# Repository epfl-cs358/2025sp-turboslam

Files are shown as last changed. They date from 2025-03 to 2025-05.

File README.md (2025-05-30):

# CS-358 - Making Intelligent Things 2025 Spring

## Project: TurboSLAM - Fast Autonomous Car using Simultaneous Localization and Mapping

TLDR: If you just want to run the thing, see section [3D SLAM (LiDAR odometry only)](#3d-slam-lidar-odometry-only).

## Contributors

- Vincent Palma
- Loris Baldisserotto
- Ivan Dylevskiy
- Ilian Changkakoti
- Sarah Lim

[Google Doc](https://docs.google.com/document/d/1Hz-CrI_mGBuuY4Cr6uao3CeAetyIk8hIU1p6bzpezqY/edit?usp=sharing)

[Project Proposal](https://www.overleaf.com/read/mtyzjbnkwfxt#540f41)

## Project Overview

This project aims to develop an autonomous system for Simultaneous Localization and Mapping (SLAM) using a 2D LiDAR sensor mounted on a servo motor. The system is designed to map an environment and navigate to given coordinates while avoiding obstacles. The project is based on modifying a **Tamiya Blitzer Beetle** RC car, replacing its original control system with an ESP32 microcontroller.

## Table of Contents

- [Description](#description)
- [User Stories](#user-stories)
- [Component List](#component-list)
- [First Idea of the Mechanical Build](#first-idea-of-the-mechanical-build)
- [How to Assemble](#how-to-assemble)
- [How to Run](#how-to-run)
- [Software](#software)
- [Expected Challenges & Solutions](#expected-challenges--solutions)
- [Evaluation Metrics](#evaluation-metrics)
- [Bill of Materials](#bill-of-materials)

## Description

The system consists of two main phases:

1. **Mapping Phase:** The robot explores the environment while the LiDAR sensor scans at multiple angles using a servo motor, creating a 3D map from 2D slices.

2. **Navigation Phase:** The system autonomously moves towards a user-specified target, avoiding dynamic obstacles in real-time.

The **ESP32** microcontroller handles remote communication and data processing, making the project a cost-effective solution for indoor and outdoor navigation applications.

## Component List

| Component | Info |
| --- | --- |
| Tamiya Blitzer Beetle | [Manual](https://www.tamiyausa.com/media/files/58502ml-829-5367.pdf) |
| RPLIDAR C1 | [Datasheet](https://d229kd5ey79jzj.cloudfront.net/3157/SLAMTEC_rplidar_datasheet_C1_v1.0_en.pdf), [SDK](https://github.com/Slamtec/rplidar_sdk), [Wiki](https://www.waveshare.com/wiki/RPLIDAR_C1) |
| ESP32-S3 Microcontroller (x2) | [Datasheet](https://cdn-shop.adafruit.com/product-files/5477/esp32-s3_datasheet_en.pdf) |
| DMS15 Servo (x2) | [Wiki](https://wiki.dfrobot.com/DSS-M15S_270%C2%B0_15KG_DF_Metal_Servo_with_Analog_Feedback_SKU__SER0044) |
| BNO086 IMU | [Datasheet](https://docs.sparkfun.com/SparkFun_VR_IMU_Breakout_BNO086_QWIIC/assets/component_documentation/BNO080_085-Datasheet_v1.16.pdf) |
| AS5600 Encoder | [Datasheet](https://files.seeedstudio.com/wiki/Grove-12-bit-Magnetic-Rotary-Position-Sensor-AS5600/res/Magnetic%20Rotary%20Position%20Sensor%20AS5600%20Datasheet.pdf) |
| HC-SR04 Ultrasonic sensor | [Datasheet](https://handsontec.com/dataspecs/sensor/SR-04-Ultrasonic.pdf) |
| NEO-6M-V2 GPS | [Datasheet](https://content.u-blox.com/sites/default/files/products/documents/NEO-6_DataSheet_%28GPS.G6-HW-09005%29.pdf) |
| 540J Motor | [Datasheet](https://asset.conrad.com/media10/add/160267/c1/-/en/001385115DS01/adatlap-1385115-540-es-motor-reely-532114c.pdf) |
| THW-1060-RTR ESC | [Datasheet](https://www.hobbywing.com/en/uploads/file/20221015/f60b7ebe160a7b283927ae8916d36763.pdf) |
| LM2596 Buck converter | [Datasheet](https://www.ti.com/lit/ds/symlink/lm2596.pdf) |
| 7.2V Battery | [Product Page](https://www.galaxus.ch/fr/s5/product/gens-ace-modelisme-dune-batterie-720-v-5000-mah-batterie-rc-9459930) |

## First Idea of the Mechanical Build

The original car chassis was unsuitable for mounting sensors, so we built a three-layer structure:

### Base Layer: Chassis

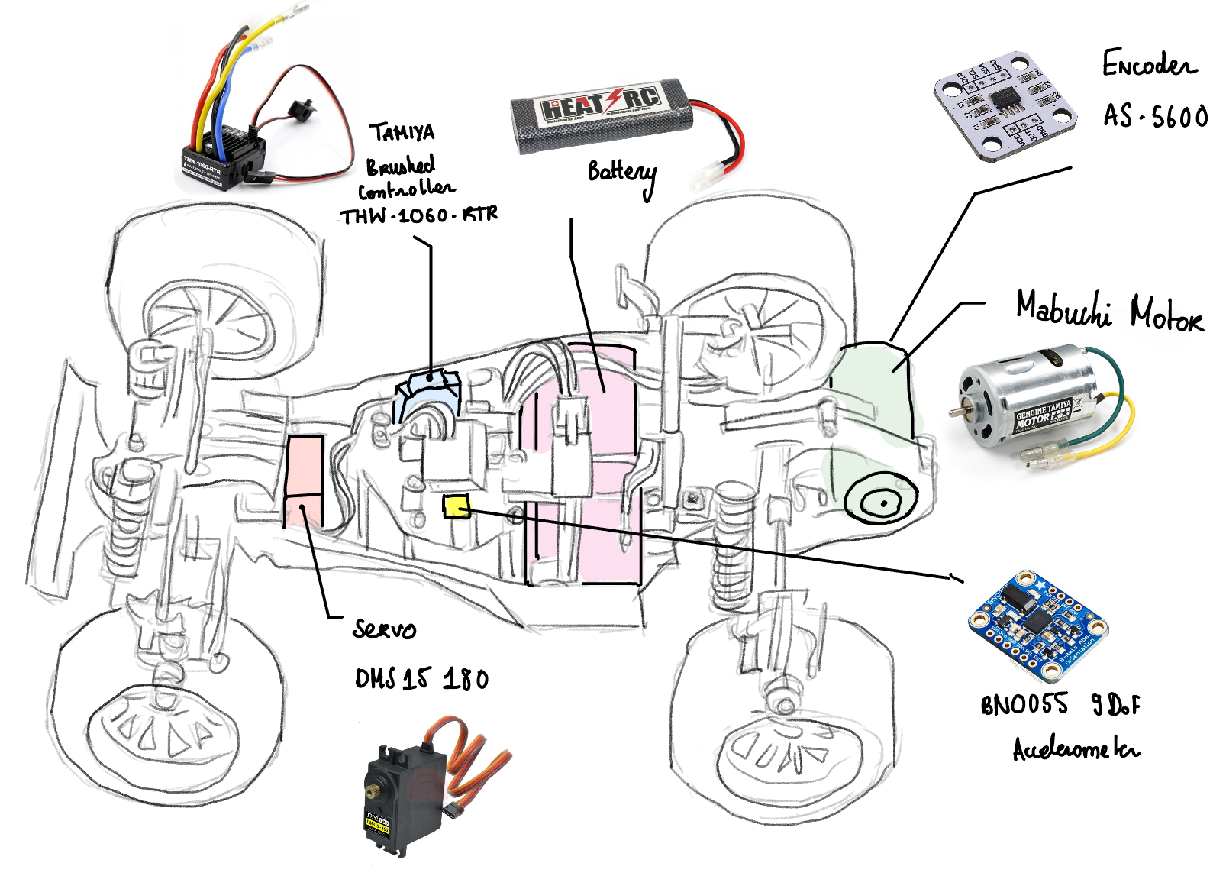
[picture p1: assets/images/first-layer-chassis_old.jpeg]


### Middle Layer: Microcontroller & Electronics Mount

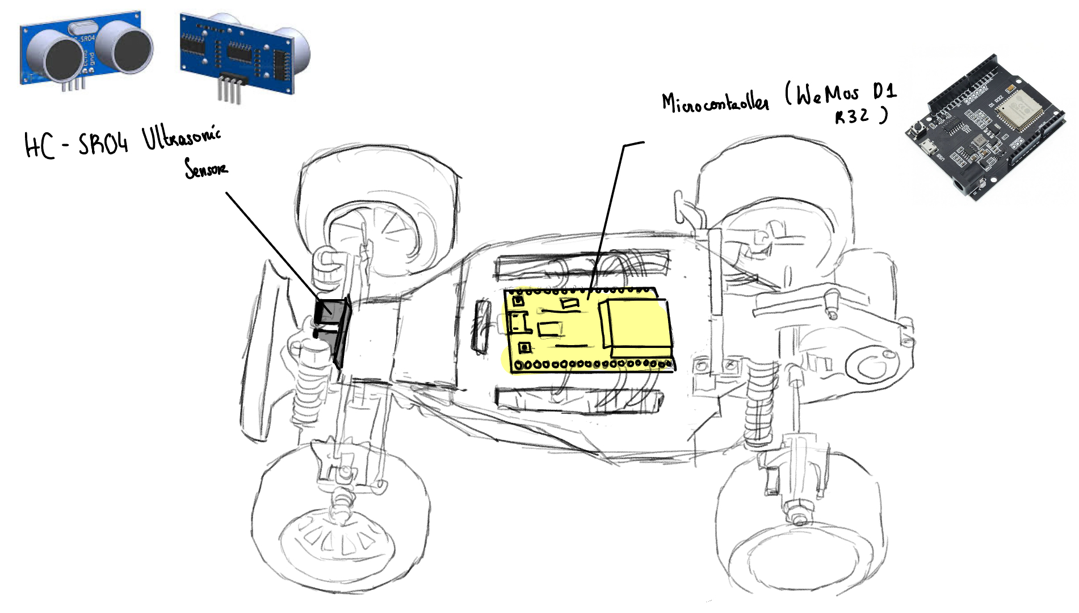
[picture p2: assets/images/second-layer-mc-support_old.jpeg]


### Top Layer: LiDAR Mount (Servo-tilted 2D LiDAR for 3D mapping)

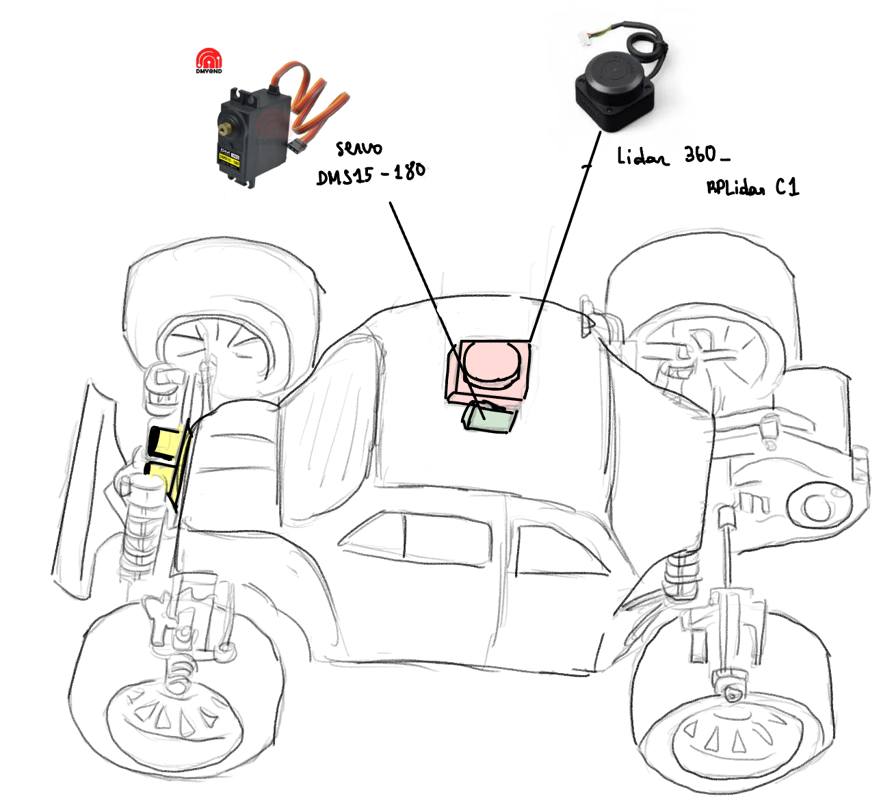
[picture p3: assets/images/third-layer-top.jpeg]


## How to Assemble

### STEP 1/8: Build the Car

Since we ordered the car, we don't have to make all its components by ourselves, but rather simply put everything together. To do this, we follow the instructions from the [Tamiya Blitzer Beetle manual](https://www.tamiyausa.com/media/files/58502ml-829-5367.pdf). The goal here is to have the minimal mechanical build, so that it can at least drive. Therefore, we should skip the carcass section and we will probably never need it at all, as it will be more of a problem than anything. The carcass doesn't have a flat surface for the lidar mount. Instead, we are going to use the layer platform, where most of the components will be mounted.

At this stage, the first servo motor for steering and the battery are mounted inside the chassis. From now on, the main part will be to attach the mounts for different sensors and actuators. All the pieces to 3D-print are available in the design/3d_files folder.

### STEP 2/8: Layer Platform

This is the basis for most of our components, including the lidar mount. The photo is _outdated_, but the CAD is the final version. We had to change the holes a few times, because we were changing sensors throughout the semester.

<div>
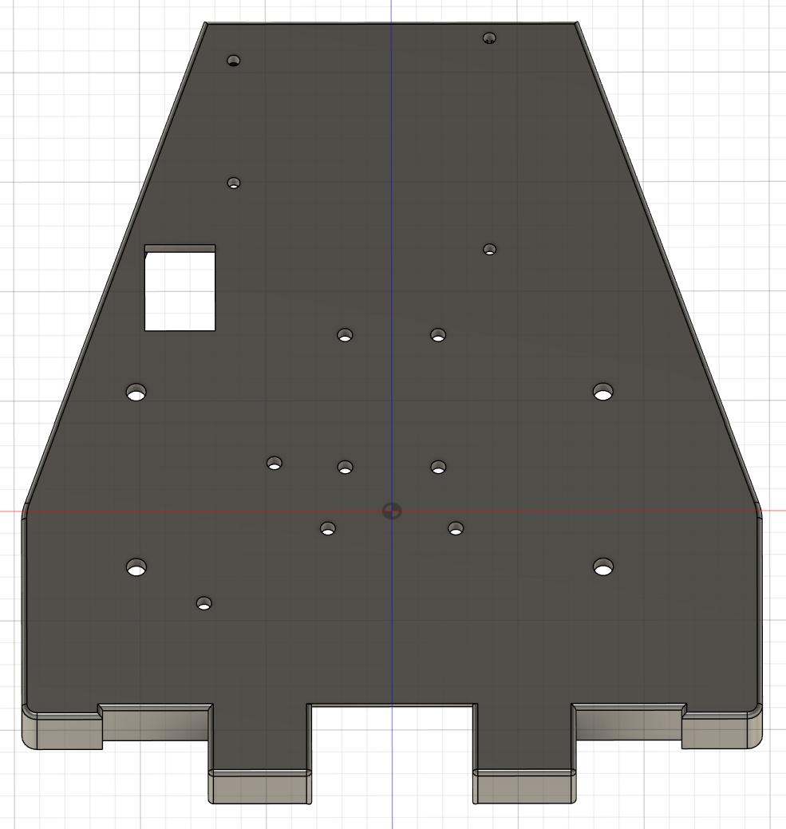
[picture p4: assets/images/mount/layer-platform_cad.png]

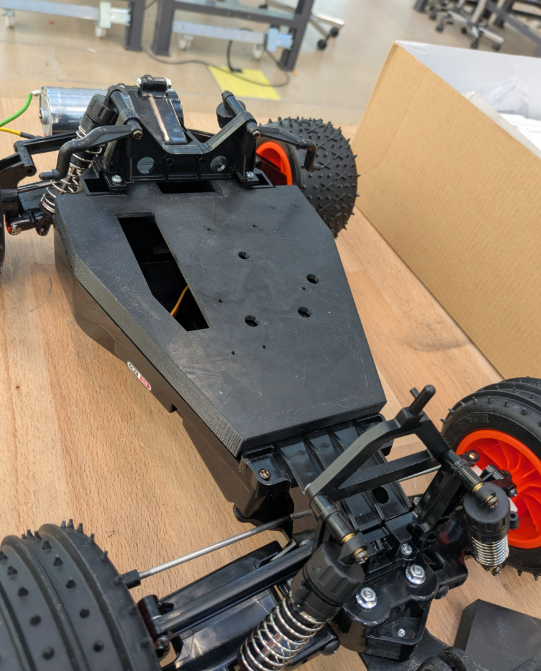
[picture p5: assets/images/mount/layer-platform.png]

</div>

After fixing it to the car, the servo for the steering will stay inside. Make sure to bring out its cables through the rectangular hole, so that later it can be connected to the microcontroller.

### STEP 3/8: Microcontroller Mount

We decided to use **two microcontrollers** for efficiency.

<div>
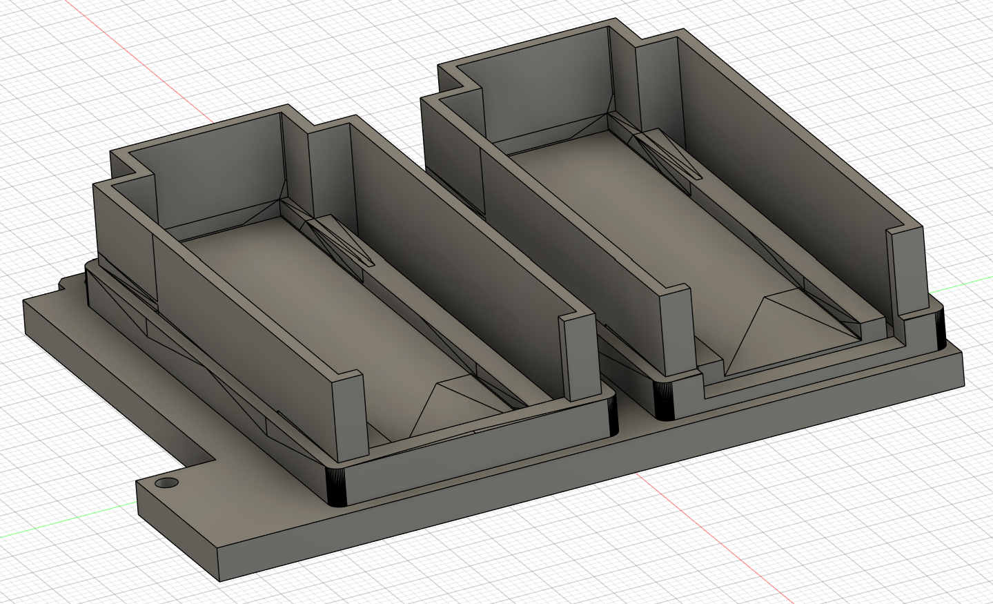
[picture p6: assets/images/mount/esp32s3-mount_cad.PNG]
  
  
</div>

### STEP 4/8: Ultrasonic Sensor Mount



### STEP 5/8: Encoder Mount

<div>
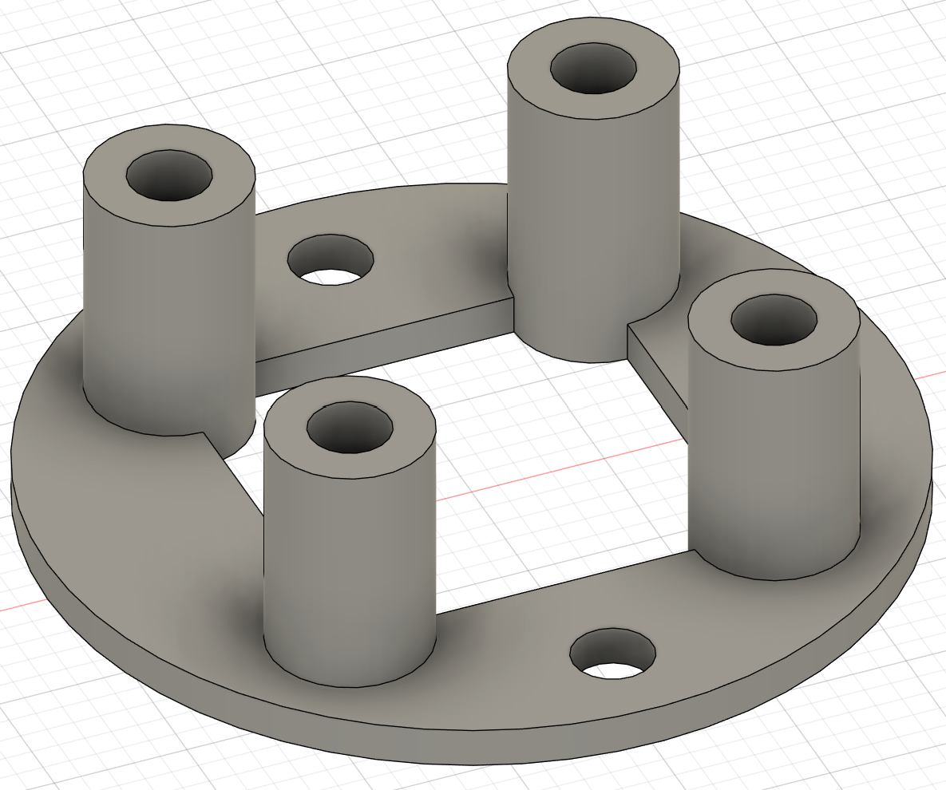
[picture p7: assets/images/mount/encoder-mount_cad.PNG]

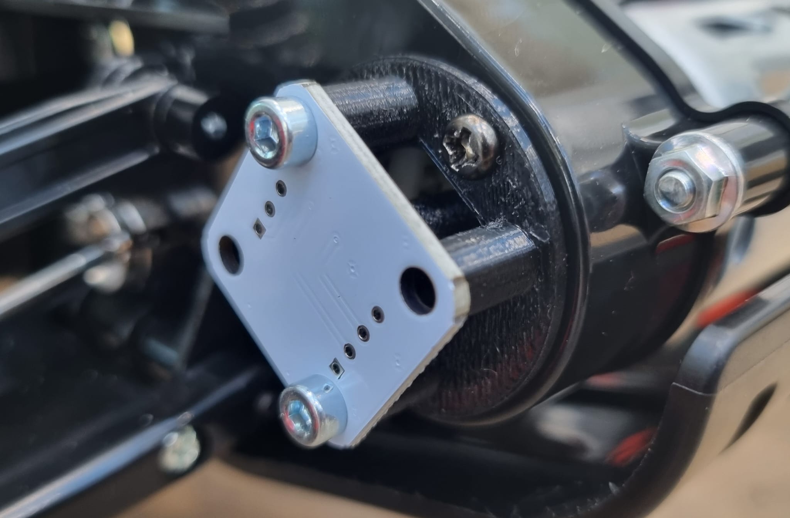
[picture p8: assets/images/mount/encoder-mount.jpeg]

</div>

### STEP 6/8: LiDAR Mount

As we explained earlier, the LiDAR is going to be tilted for the 3D scan. This mount will make it easy to do. It consists of two walls and a tilting platform in between:

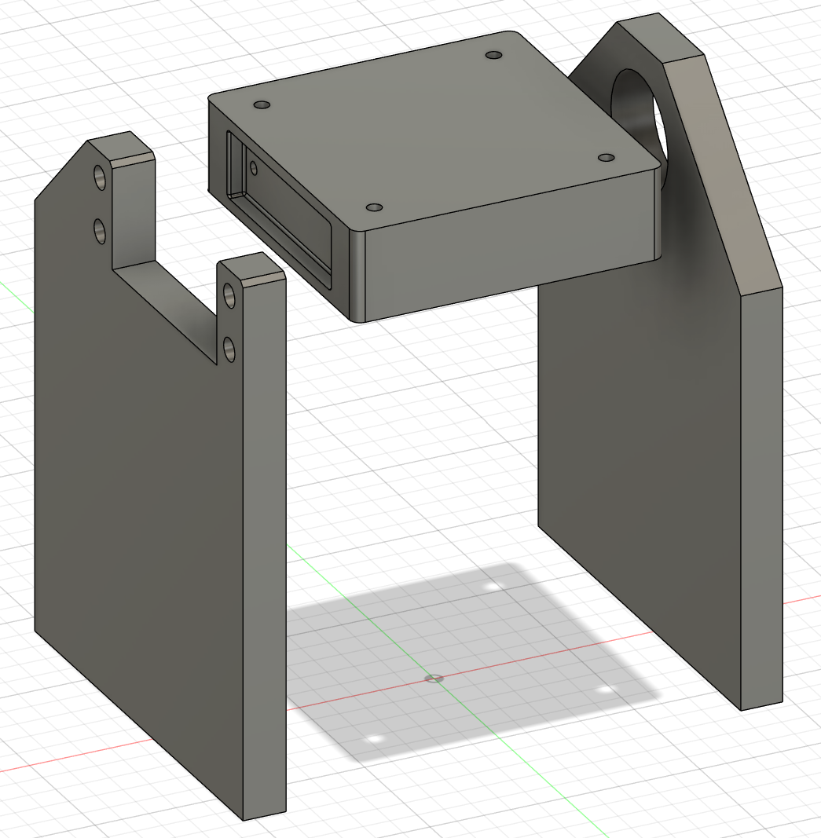
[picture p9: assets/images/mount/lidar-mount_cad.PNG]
 <br>

On the left wall, the servo motor will move the platform. For the right wall, we'll need some additional pieces from the mechanical workshop to provide more stability:

- **M6 Ball bearing** (6 x 22 x 7mm)
- **M6 Screw** (35mm)
- **M6 Washer** (6.4 x 12 x 1.6mm)
- **M6 Locknut** (8mm width)
- **M6 Threaded insert** (8.7mm diameter, 12.7mm length)

To assemble these small pieces:

- Put the **screw** inside the **bearing**
- On the other side, insert the **washer**, then the **locknut**
- **Press fit** the bearing into the right wall (the hole might be a bit too small after the printing, so it needs to be filed first)
- Insert the **threaded insert** into the tilting platform on the right side

Now, both walls with the servo and the bearing can be attached to the tilting platform:

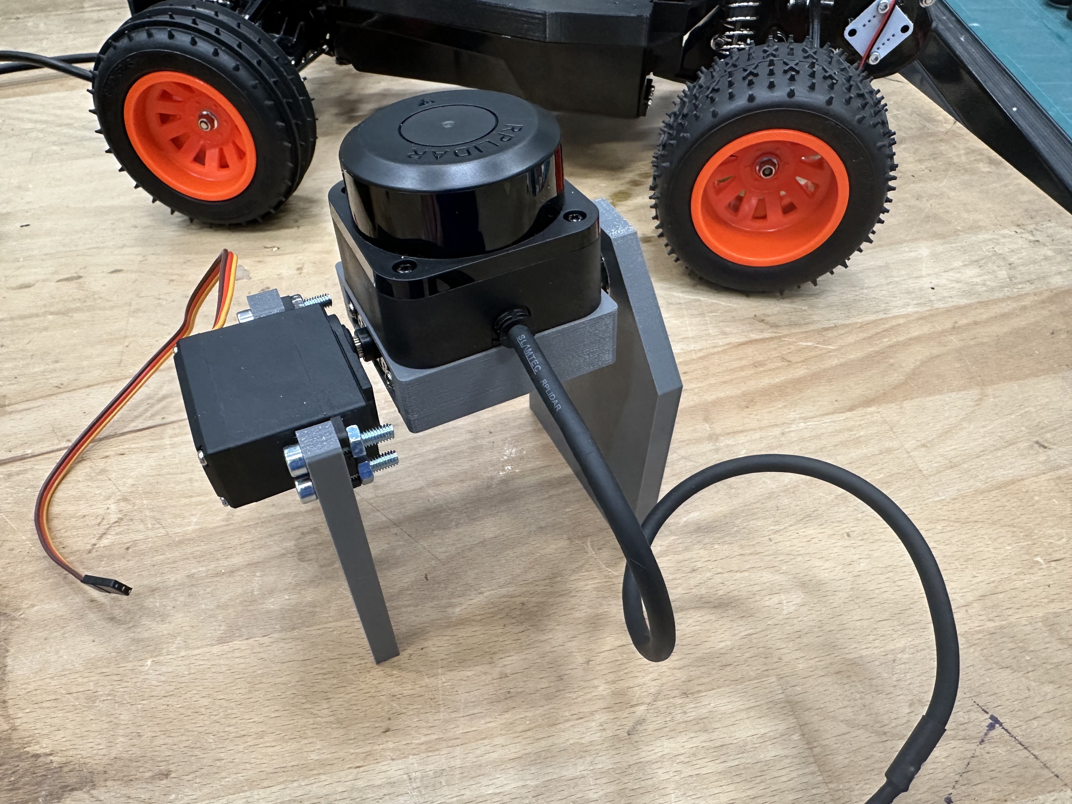
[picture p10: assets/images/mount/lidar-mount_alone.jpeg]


### STEP 7/8: Attach all the Remaining Mounts

Screw most of the sensors/mounts to the layer platform as shown on this image:

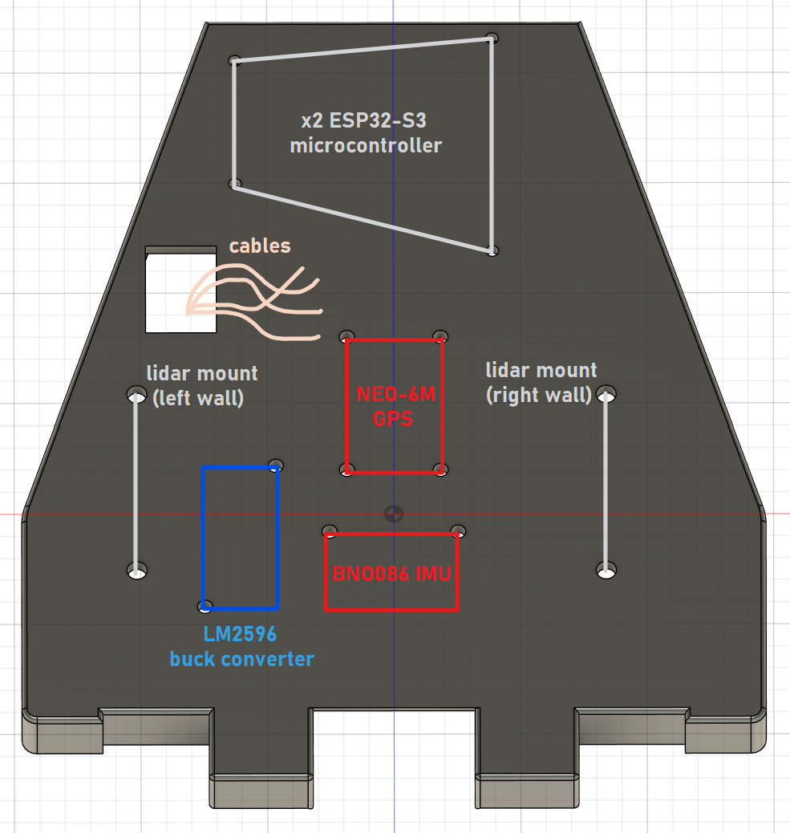
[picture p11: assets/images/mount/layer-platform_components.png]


Most of them use M3 screws.

This is what it should look like:



### STEP 8/8: Wiring

Follow the wiring from this circuit diagram:

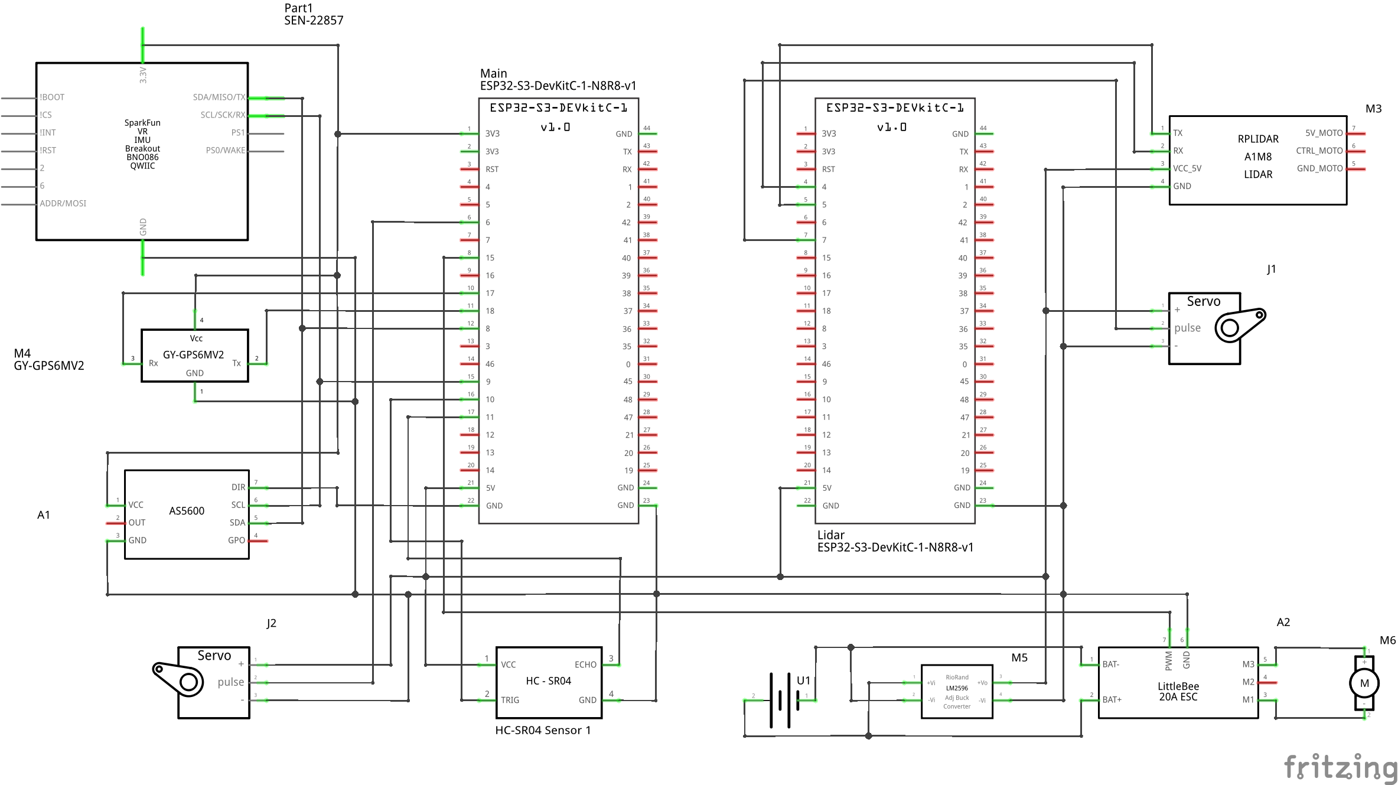
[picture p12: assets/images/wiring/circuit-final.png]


## Communication

Since the 3D SLAM algorithm is fairly resource intensive, we cannot directly run it on the ESP32-S3. but need first to send the data of the sensors to the

laptop, where the computations will happen. Luckily, this is a fairly straightforward process with ROS2 (note that the ESP32 and the laptop have to be connected to theme Wi-Fi in order for this to work). A topic was created for each sensor, and on these topics data was published using rclc_publish. The main limitation here was the achievable publishing rate for the different sensors. Since the rclc_publish method is "fairly heavy" (I mean by that that it is not as optimal as a complete implementation by hand and correctly optimized), the frequency we managed to achieve is definitely sub-optimal, though still usable. Here is a list of all the sensors and achieved frequency :

- IMU: 20 Hz with ultrasonic running (30 Hz without ultrasonic)
- LIDAR: 8-10 Hz
- Lidar servo: 20 Hz (this is not a sensor, though we still needed that live angle for the lidar to transform the 2D points of the lidar into 3D)
- Ultrasonic: 20 Hz (with IMU)

Note that there are other topics for the motor and the servo responsible for the direction, though these ones were not as essential to optimize for the algorithm to work.

It is also essential to mention that in order to achieve these frequencies, 2 ESP32-S3s with 8 MB of additional PSRAM were needed, as well as a complete and optimized implementation using FreeRTOS utilizing both cores of the microcontroller.

## ROS2 Tips and Tricks

If you want to use ROS for your project, we highly recommend a raspberry PI instead of microcontrollers (and if you choose microcontrollers choose something more "beefy" than a Wemos d1 r32). If you still want to go the path we did, micro-ROS is what you need. Settle on the last ROS2 version compatible with micro-ROS (Humble at the time of writing this), and read the [docs](https://docs.ros.org/en/humble/index.html) to get familiar.

If you don't have the specific OS required by the ROS2 version (ubuntu 22.04 in the case of Humble), Docker is a perfectly fine option, AS LONG AS YOU ARE ON LINUX (the --net=host option is essential for topics published inside the container to be available on the host and vice-versa).

To get UDP communication working with the esp32, look at our code at `esp32/microros_rplidar_c1/main.cpp` (note that you need to run microros-agent on the laptop, details are written in a README somewhere). It is also good practice to use FreeRTOS when you have more than one component (see the same file) and will simplify your life a lot.

Mind that SUBSCRIBING (publishing works fine for any data type) to messages of data types more complex than simple `Int32` or `Float32` (for example `Joy` in our case..) is likely to not work with micro-ROS.

One really practical thing about ROS are bag files, they allow to record the whole system running and then play it back later at home for debugging.

Read the different READMEs scattered around the repo's subfolders, there is a lot of info there that I probably forgot to write here.

## Issues

We'll list here the main issues encountered during this project, as well as how we tried to fix them.

1. The first microcontroller we chose, the Wemos D1 R32, was not a fitting choice due to its lack of processing power and restraint RAM (without any possibility to add more on top). Instead, we bought 2 ESP32-S3s with 16 MB of flash, 8 MB of PSRAM, and much faster processing power.

2. The first algorithm we wanted to use (LIO-SAM) required the IMU to publish at 200 Hz (whereas the one we had at the time could only output 100 Hz at best). We decided to buy a new one, the BNO086, which can output at 400 Hz (note that this was actually completely useless in the end).

3. Even while using both ESP32-S3s (at the same time), the best rate we could achieve for the IMU was 30 Hz. There is actually not much we could do here, since this is mainly limited by the rclc_publish method of ROS2 (see the communication section).

4. I2C communication with the IMU is unstable; it works sometimes but not right after. This issue, which persisted throughout the whole project, also prevented us from calibrating the IMU correctly.

5. Having a complete ROS 2 Humble setup on everyone's machine was also quite the challenge. In the team everyone used a different OS, and ROS2 Humble needed specifically Ubuntu 22.04 in order to work. Docker was needed to run an instance of ROS 2 Humble on other Linux distros (the Docker command does not work on Windows without WSL).

Note: It is probably useful to mention that 3D Lidar mapping is not the most fitting project to realize on microcontrollers due to their lack of processing power. A Raspberry Pi would have probably (and most certainly) been a better and more optimal choice.

## 3D SLAM (LiDAR odometry only)

Here are everything you need to run to get the expected results.

DISCLAIMER: the following commands are only possible if you have ros2 humble installed on your system (which needs to be Ubuntu 22.04 [^1]).

First upload the code on the correct ESP's. The main final code is a platformio project under `esp32/microros_rplidar_c1`. Now in the file `src/main.cpp` change the test bits at the top before uploading in the following way:

1. For the first ESP (the one not connected to the lidar), enable the IMU, ultrasonic, servo_dir and motor_cmd. Then upload on the first ESP.

2. For the second ESP, enable the servo_lid, lidar and servo_angle_pub, the upload.

NOTE: you also need to create a `credentials.h` file for that and be connected on same WiFI with the laptop, please refer to `esp32/microros_rplidar_c1/README.md`.

After that in a terminal run:

```
docker run -it --rm --net=host microros/micro-ros-agent:humble udp4 --port 8888 -v6
```

This start the communication between the laptop and both of the esp32's. To check that it works as expected run (in an other terminal):

```
ros2 topic list
```

and after (as an example):

```
ros2 topic echo /scan
```

You should see some data arriving.

Afet that, go into `backend/ros2_ws/src/teleop_keyboard` and run the script to be able to control the car using WASD[^2]:

```
python Teleop.py
```

IMPORTANT: for the next two steps you need to be in `backend/ros2_ws` and have run `colcon build --packages-select tilt_lidar_node loam_back_and_forth` already.
IMPORTANT2: the base frame is "base_link" and not "world" for Rviz, if for some reason you don't see any output in Rviz but `/scan` outputs correctly, check that the parameter `Global Options -> Fixed Frame` is set to `base_link`.

In one terminal (this package projects the 2d LaserScans from topic `/scan` according to the current servo angle from topic `/lidar_servo_angle` to topic `/point_cloud`):

```
source install/setup.zsh
ros2 launch tilt_lidar_node view_tilt_lidar_launch.py
```

Then, in another terminal (this packages just takes the rings and publishes a full sweep, i.e. proper 3d scan as if we had a real 3d lidar like Velodyne, to topic `/full_scan`):

```
source install/setup.zsh
ros2 launch loam_back_and_forth loam_back_and_forth_launch.py
```

and in last terminal (this is a [separate project](https://github.com/MOLAorg/mola) that does SLAM based on 3d scans):

```
ros2 launch mola_lidar_odometry ros2-lidar-odometry.launch.py \
   lidar_topic_name:=full_scan \
   ignore_lidar_pose_from_tf:=True \
   publish_localization_following_rep105:=False
```

## Bill of Materials

| Category | Quantity | Cost (CHF) | Info |
| --- | --- | --- | --- |
| Tamiya Blitzer Beetle | 1 | 129 | [Manual](https://www.tamiyausa.com/media/files/58502ml-829-5367.pdf) |
| RPLIDAR C1 | 1 | 79.90 | [Datasheet](https://d229kd5ey79jzj.cloudfront.net/3157/SLAMTEC_rplidar_datasheet_C1_v1.0_en.pdf), [SDK](https://github.com/Slamtec/rplidar_sdk), [Wiki](https://www.waveshare.com/wiki/RPLIDAR_C1) |
| Wemos D1-R32 Microcontroller | 1 | 4.0 | |
| DMS15 Servo | 2 | 5.0 | [Wiki](https://wiki.dfrobot.com/DSS-M15S_270%C2%B0_15KG_DF_Metal_Servo_with_Analog_Feedback_SKU__SER0044) |
| BNO055 9DoF IMU | 1 | 19.90 | [Product Page](https://www.bastelgarage.ch/bno055-capteur-intelligent-a-9-axes?search=9dof), [Datasheet](https://cdn-shop.adafruit.com/datasheets/BST_BNO055_DS000_12.pdf) |
| AS5600 Encoder | 1 | 3.90 | [Datasheet](https://files.seeedstudio.com/wiki/Grove-12-bit-Magnetic-Rotary-Position-Sensor-AS5600/res/Magnetic%20Rotary%20Position%20Sensor%20AS5600%20Datasheet.pdf) |
| HC-SR04 Ultrasonic sensor | 1 | 2.0 | [Datasheet](https://handsontec.com/dataspecs/sensor/SR-04-Ultrasonic.pdf) |
| NEO-6M-V2 GPS | 1 | 13.50 | [Datasheet](https://content.u-blox.com/sites/default/files/products/documents/NEO-6_DataSheet_%28GPS.G6-HW-09005%29.pdf) |
| 7.2V Battery | 1 | 23.90 (+ 5.0) | [Product Page](https://www.galaxus.ch/fr/s5/product/gens-ace-modelisme-dune-batterie-720-v-5000-mah-batterie-rc-9459930) |

Note that this is not our final component list, but rather what we ordered at the beginning of the project. You can find the final list in the [Component List](#component-list).

## Related Projects

- [Laser Scan to Point Cloud](https://github.com/carlosmccosta/laserscan_to_pointcloud?tab=readme-ov-file)
- [ESP32 with ESC Controller](https://github.com/Tales-sv/Esp32-ESC_Controler)
- [LiDAR-Based SLAM](https://github.com/w111liang222/lidar-slam-detection)
- [SLAM Using 2D LiDAR](https://github.com/meyiao/LaserSLAM)

---

**MIT - Spring 2025**

[^1]: It should be doable to run most of the components in Docker containers but Rviz would still need to be run on the host, or use the host's X11 server, to see the GUI.
[^2]: Note that when turning the car (pressing A or D) a lot of message are transmitted to the car ros node, and thus it makes the LiDAR output stop for a while because of the lack of throughput.

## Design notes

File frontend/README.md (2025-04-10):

# Frontend

Created following https://ui.shadcn.com/docs/installation/vite.

To add new UI components (buttons, sliders, etc.), follow instructions at https://ui.shadcn.com/docs/components/.

## Get Started

Install Node.js an pnpm.

Run `pnpm install` to install dependencies.

Run `pnpm run dev` to start the dev server.

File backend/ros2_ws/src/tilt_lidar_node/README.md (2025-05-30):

Takes LaserScan messages from topic `/scan` and servo angle (Int32) from topic `/lidar_servo_angle` and publishes a 3D point cloud (PointCloud2) in topic `/point_cloud`.

Assumes that the servo angle is in degrees and that the horizontal position is 90 degrees (range 0–180).

# TLDR: one command to run

```bash
ros2 launch tilt_lidar_node view_tilt_lidar_launch.py
```

or if using ros bag recording:

```bash
ros2 launch tilt_lidar_node view_tilt_lidar_sim_launch.py
```

# Manual way

## Run on recorded bag file

In directory `backend/bag_files`, run:

```bash
ros2 bag play -l lidar_servo_imu_pcl_slow_10hz_5hz_10hz --clock
```

in another terminal:

```bash
ros2 run tilt_lidar_node tilt_lidar_node \    
  --ros-args -p use_sim_time:=true
```

## Run on live data

```bash
ros2 run tilt_lidar_node tilt_lidar_node
```

## Visualize the point cloud

```bash
ros2 run rviz2 rviz2
```

Add a new display (CTRL + N) of type `PointCloud2` and set the topic to `/point_cloud`.

Set Global Options -> Fixed Frame to `base_link`.

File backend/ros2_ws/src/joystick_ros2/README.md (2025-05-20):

## TurboSLAM instructions

Go to ros2_ws/

```bash
colcon build --packages-select joystick_ros2
source install/setup.bash
ros2 run joystick_ros2 joystick_ros2
```
Change throttle time in line 183 of joystick_ros2.py if needed.

# joystick_ros2
The first joystick driver for ROS2 created from scratch to support all platforms: Linux, OS X, Windows.

## Install
```
# with ROS2 already sourced
$ cd <ros2_workspace>/src
$ git clone https://github.com/FurqanHabibi/joystick_ros2
$ cd ..
$ ament build

# for Linux / OS X
$ source install/local_setup.bash

# for Windows
$ call install/local_setup.bat
```

## Usage
- Plug in the joystick
- Run the node with below command
    ```
    $ ros2 run joystick_ros2 joystick_ros2
    ``` 

## Supported joysticks
Windows:

    - All Xinput Controller

Linux, Mac OSX:

    - PS4 Controller
    - Logitech F710
    - Xbox One Controller

## ROS2 Node
### Published Topics
- joy ([sensor_msgs/Joy](https://github.com/ros2/common_interfaces/blob/master/sensor_msgs/msg/Joy.msg))

    Outputs the joystick state.
### Parameters
TODO : use ros2 param when it becomes available on rclpy.

- ~deadzone (double, default: 0.05)

    Amount by which the joystick has to move before it is considered to be off-center. This parameter is specified relative to an axis normalized between -1 and 1. Thus, 0.1 means that the joystick has to move 10% of the way to the edge of an axis's range before that axis will output a non-zero value. Linux does its own deadzone processing, so in many cases this value can be set to zero.

- ~autorepeat_rate (double, default: 0.0 (disabled))

    Rate in Hz at which a joystick that has a non-changing state will resend the previously sent message.

- ~coalesce_interval (double, default: 0.001)

    Axis events that are received within coalesce_interval (seconds) of each other are sent out in a single ROS message. Since the kernel sends each axis motion as a separate event, coalescing greatly reduces the rate at which messages are sent. This option can also be used to limit the rate of outgoing messages. Button events are always sent out immediately to avoid missing button presses.

## Notes
### OS X Permissions
You probably have to use the settings application to allow gamepad input on OS X.
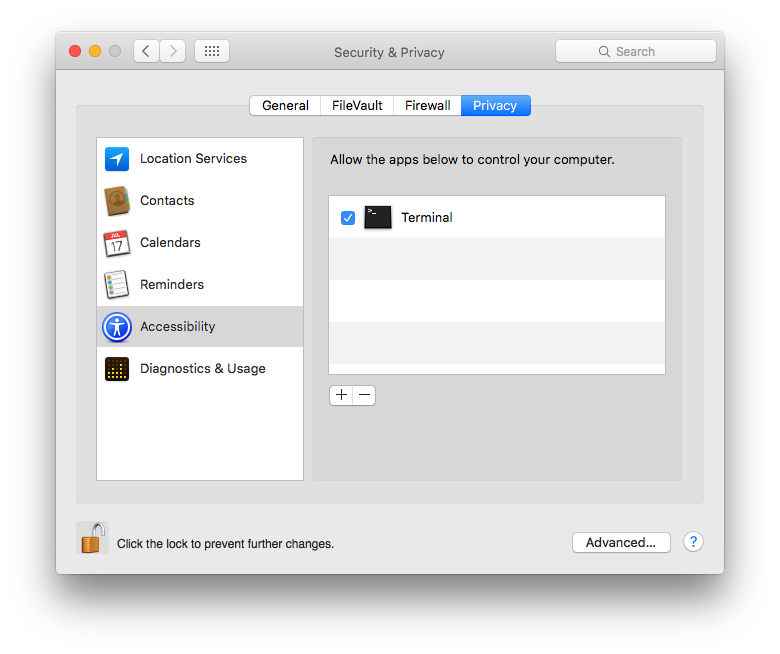
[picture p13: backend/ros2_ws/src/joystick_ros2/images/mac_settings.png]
Mac Settings


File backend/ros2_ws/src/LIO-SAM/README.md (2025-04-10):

This is the ros2 branch of [LIO-SAM](https://github.com/TixiaoShan/LIO-SAM/c) at commit [08af3f3
](https://github.com/TixiaoShan/LIO-SAM/commit/08af3f32f01725372d4269838dc44c19c6d9e76b).

# LIO-SAM

**A real-time lidar-inertial odometry package. We strongly recommend the users read this document thoroughly and test the package with the provided dataset first. A video of the demonstration of the method can be found on [YouTube](https://www.youtube.com/watch?v=A0H8CoORZJU).**

<p align='center'>
    
</p>

<p align='center'>
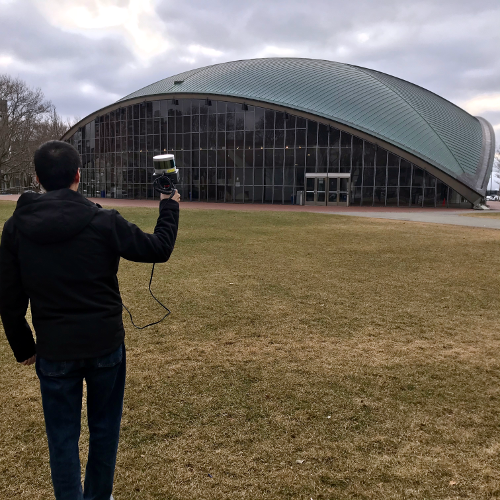
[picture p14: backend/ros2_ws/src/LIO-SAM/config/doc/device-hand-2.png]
    
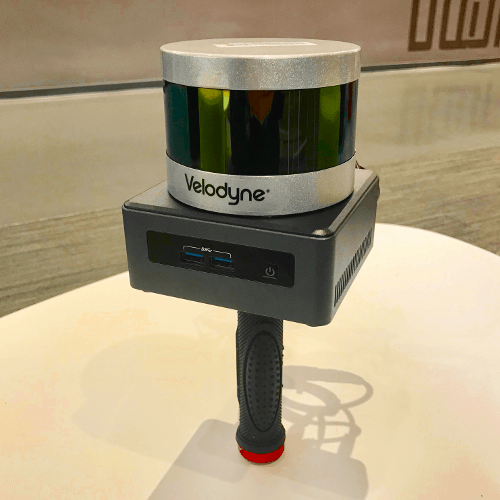
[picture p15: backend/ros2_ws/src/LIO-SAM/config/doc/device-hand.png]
    
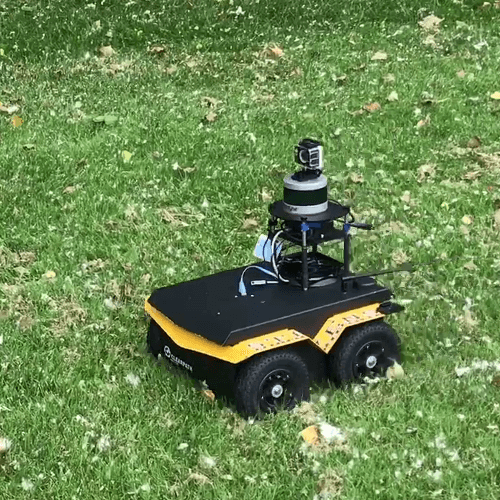
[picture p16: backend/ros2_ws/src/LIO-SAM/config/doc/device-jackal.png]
    
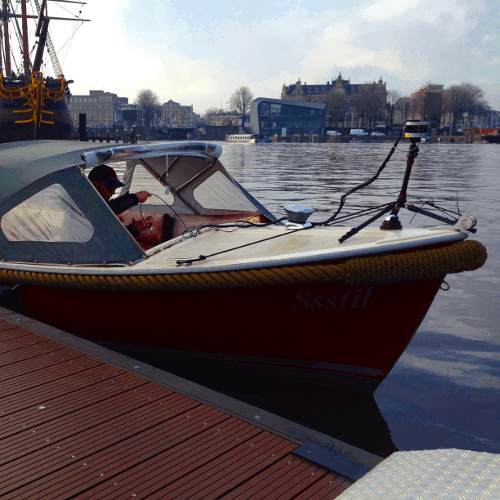
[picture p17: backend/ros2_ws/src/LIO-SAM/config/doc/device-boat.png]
    
</p>

## Menu

  - [**System architecture**](#system-architecture)

  - [**Notes on ROS2 branch**](#notes-on-ros2-branch)

  - [**Package dependency**](#dependency)

  - [**Package install**](#install)

  - [**Prepare lidar data**](#prepare-lidar-data) (must read)

  - [**Prepare IMU data**](#prepare-imu-data) (must read)

  - [**Sample datasets**](#sample-datasets)

  - [**Run the package**](#run-the-package)

  - [**Other notes**](#other-notes)

  - [**Issues**](#issues)

  - [**Paper**](#paper)

  - [**TODO**](#todo)

  - [**Related Package**](#related-package)

  - [**Acknowledgement**](#acknowledgement)

## System architecture

<p align='center'>
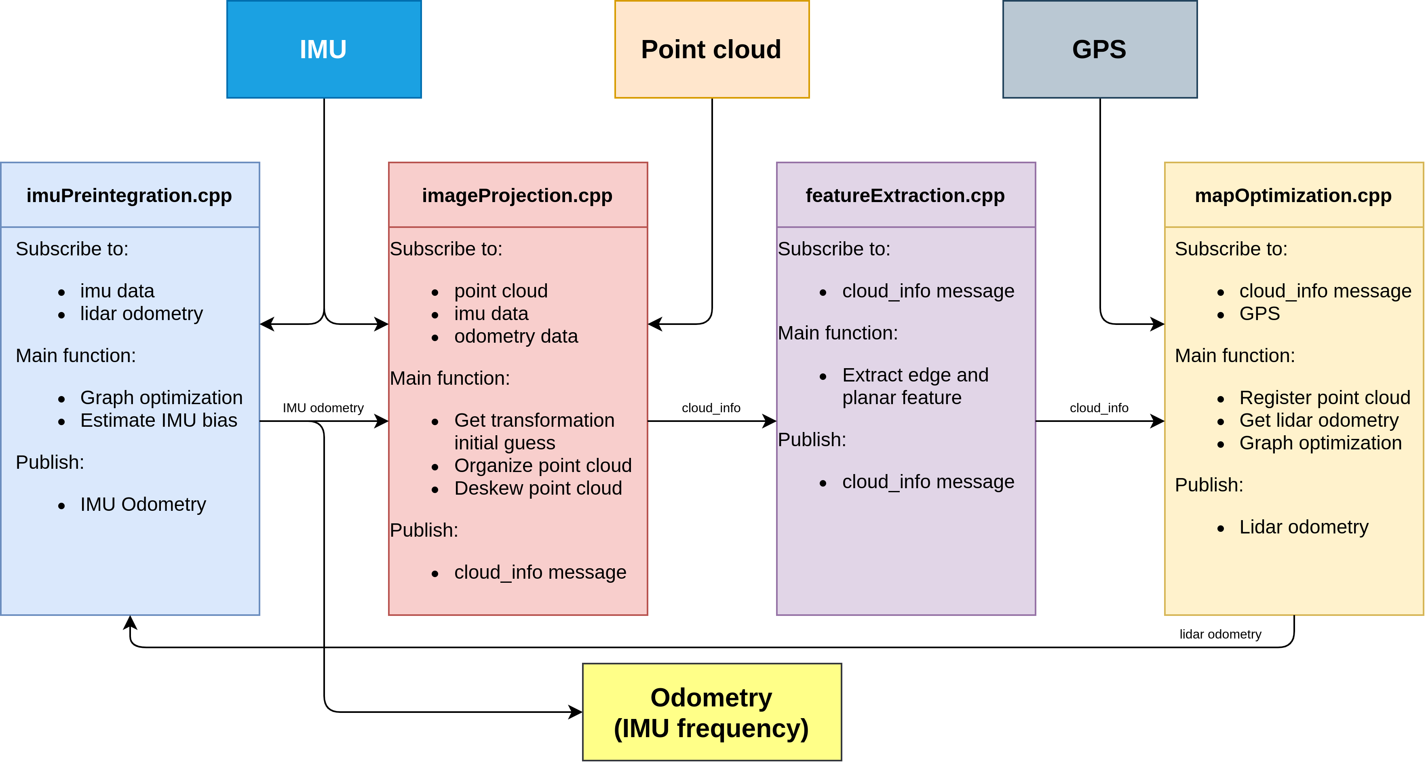
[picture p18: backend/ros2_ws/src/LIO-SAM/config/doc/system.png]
    
</p>

We design a system that maintains two graphs and runs up to 10x faster than real-time.
  - The factor graph in "mapOptimization.cpp" optimizes lidar odometry factor and GPS factor. This factor graph is maintained consistently throughout the whole test.
  - The factor graph in "imuPreintegration.cpp" optimizes IMU and lidar odometry factor and estimates IMU bias. This factor graph is reset periodically and guarantees real-time odometry estimation at IMU frequency.

## Notes on ROS2 branch

There are some features of the original ROS1 version that are currently missing in this ROS2 version, namely:
- Testing with Velodyne & Livox lidars and Microstrain IMUs
- A launch file for the navsat module/GPS factor
- The rviz2 configuration misses many elements

This branch was tested with Ouster lidars, Xsens IMUs and SBG-Systems IMUs using the following ROS2 drivers:
- [ros2_ouster_drivers](https://github.com/ros-drivers/ros2_ouster_drivers)
- [bluespace_ai_xsens_ros_mti_driver](https://github.com/bluespace-ai/bluespace_ai_xsens_ros_mti_driver)
- [sbg_ros2_driver](https://github.com/SBG-Systems/sbg_ros2_driver)

In these tests, the IMU was mounted on the bottom of the lidar such that their x-axes pointed in the same direction. The parameters `extrinsicRot` and `extrinsicRPY` in `params.yaml` correspond to this constellation.

## Dependencies

Tested with ROS2 versions foxy and galactic on Ubuntu 20.04 and humble on Ubuntu 22.04
- [ROS2](https://docs.ros.org/en/humble/Installation.html)
  ```
  sudo apt install ros-humble-perception-pcl \
		   ros-humble-pcl-msgs \
		   ros-humble-vision-opencv \
		   ros-humble-xacro
  ```
- [gtsam](https://gtsam.org/get_started) (Georgia Tech Smoothing and Mapping library)
  ```
  # Add GTSAM-PPA
  sudo add-apt-repository ppa:borglab/gtsam-release-4.1
  sudo apt install libgtsam-dev libgtsam-unstable-dev
  ```

## Install

Use the following commands to download and compile the package.

  ```
  cd ..
  colcon build
  source install/setup.bash
  ```

## Using Docker

Build image (based on ROS2 Humble):

```
docker build -t liosam-humble-jammy .
```

Once you have the image, you can start a container by using one of the following methods:

1. `docker run`

```
docker run --init -it -d \
  --name liosam-humble-jammy-container \
  -v /etc/localtime:/etc/localtime:ro \
  -v /etc/timezone:/etc/timezone:ro \
  -v /tmp/.X11-unix:/tmp/.X11-unix \
  -e DISPLAY=$DISPLAY \
  --runtime=nvidia --gpus all \
  liosam-humble-jammy \
  bash
```

2. `docker compose`

Start a docker compose container:

```
docker compose up -d
```

Stopping a docker compose container:
```
docker compose down
```

To enter into the running container use:

```
docker exec -it liosam-humble-jammy-container bash
```
## Prepare lidar data

The user needs to prepare the point cloud data in the correct format for cloud deskewing, which is mainly done in "imageProjection.cpp". The two requirements are:
  - **Provide point time stamp**. LIO-SAM uses IMU data to perform point cloud deskew. Thus, the relative point time in a scan needs to be known. The up-to-date Velodyne ROS driver should output this information directly. Here, we assume the point time channel is called "time." The definition of the point type is located at the top of the "imageProjection.cpp." "deskewPoint()" function utilizes this relative time to obtain the transformation of this point relative to the beginning of the scan. When the lidar rotates at 10Hz, the timestamp of a point should vary between 0 and 0.1 seconds. If you are using other lidar sensors, you may need to change the name of this time channel and make sure that it is the relative time in a scan.
  - **Provide point ring number**. LIO-SAM uses this information to organize the point correctly in a matrix. The ring number indicates which channel of the sensor that this point belongs to. The definition of the point type is located at the top of "imageProjection.cpp." The up-to-date Velodyne ROS driver should output this information directly. Again, if you are using other lidar sensors, you may need to rename this information. Note that only mechanical lidars are supported by the package currently.

## Prepare IMU data

  - **IMU requirement**. Like the original LOAM implementation, LIO-SAM only works with a 9-axis IMU, which gives roll, pitch, and yaw estimation. The roll and pitch estimation is mainly used to initialize the system at the correct attitude. The yaw estimation initializes the system at the right heading when using GPS data. Theoretically, an initialization procedure like VINS-Mono will enable LIO-SAM to work with a 6-axis IMU. The performance of the system largely depends on the quality of the IMU measurements. The higher the IMU data rate, the better the system accuracy. We use Microstrain 3DM-GX5-25, which outputs data at 500Hz. We recommend using an IMU that gives at least a 200Hz output rate. Note that the internal IMU of Ouster lidar is an 6-axis IMU.

  - **IMU alignment**. LIO-SAM transforms IMU raw data from the IMU frame to the Lidar frame, which follows the ROS REP-105 convention (x - forward, y - left, z - upward). To make the system function properly, the correct extrinsic transformation needs to be provided in "params.yaml" file. **The reason why there are two extrinsics is that my IMU (Microstrain 3DM-GX5-25) acceleration and attitude have different coordinates. Depending on your IMU manufacturer, the two extrinsics for your IMU may or may not be the same**.
    - "extrinsicRot" in "params.yaml" is a rotation matrix that transforms IMU gyro and acceleometer measurements to lidar frame.
    - "extrinsicRPY" in "params.yaml" is a rotation matrix that transforms IMU orientation to lidar frame.

  - **IMU debug**. It's strongly recommended that the user uncomment the debug lines in "imuHandler()" of "imageProjection.cpp" and test the output of the transformed IMU data. The user can rotate the sensor suite to check whether the readings correspond to the sensor's movement. A YouTube video that shows the corrected IMU data can be found [here (link to YouTube)](https://youtu.be/BOUK8LYQhHs).

<p align='center'>
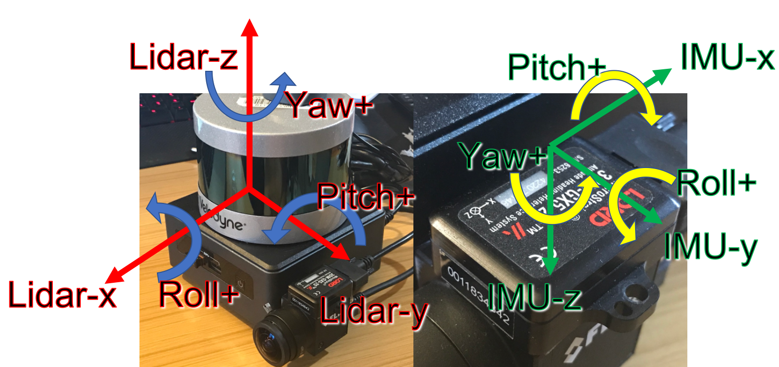
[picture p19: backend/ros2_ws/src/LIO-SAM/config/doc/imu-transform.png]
    
</p>
<p align='center'>
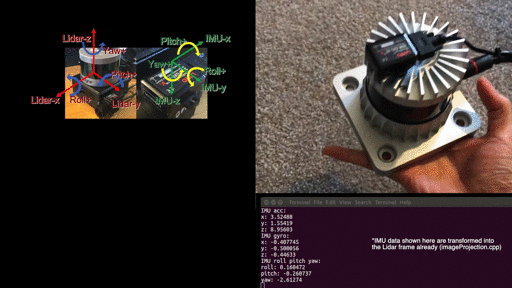
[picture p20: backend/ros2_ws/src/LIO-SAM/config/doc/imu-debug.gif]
    
</p>

## Sample datasets

For privacy reasons, no data set can currently be made available for ROS2.

README.md of the master branch contains some links to ROS1 rosbags. It is possible to use [ros1_bridge](https://github.com/ros2/ros1_bridge) with these rosbags, but verify timing behavior (message frequency in ROS2) first. Mind [DDS tuning](https://docs.ros.org/en/humble/How-To-Guides/DDS-tuning.html).

## Run the package

1. Run the launch file:
```
ros2 launch lio_sam run.launch.py
```

2. Play existing bag files:
```
ros2 bag play your-bag.bag
```

## Save map
```
ros2 service call /lio_sam/save_map lio_sam/srv/SaveMap
```
```
ros2 service call /lio_sam/save_map lio_sam/srv/SaveMap "{resolution: 0.2, destination: /Downloads/service_LOAM}"
```
## Other notes

  - **Loop closure:** The loop function here gives an example of proof of concept. It is directly adapted from LeGO-LOAM loop closure. For more advanced loop closure implementation, please refer to [ScanContext](https://github.com/irapkaist/SC-LeGO-LOAM). Set the "loopClosureEnableFlag" in "params.yaml" to "true" to test the loop closure function. In Rviz, uncheck "Map (cloud)" and check "Map (global)". This is because the visualized map - "Map (cloud)" - is simply a stack of point clouds in Rviz. Their postion will not be updated after pose correction. The loop closure function here is simply adapted from LeGO-LOAM, which is an ICP-based method. Because ICP runs pretty slow, it is suggested that the playback speed is set to be "-r 1". You can try the Garden dataset for testing.

<p align='center'>
    
    
</p>

  - **Using GPS:** The park dataset is provided for testing LIO-SAM with GPS data. This dataset is gathered by [Yewei Huang](https://robustfieldautonomylab.github.io/people.html). To enable the GPS function, change "gpsTopic" in "params.yaml" to "odometry/gps". In Rviz, uncheck "Map (cloud)" and check "Map (global)". Also check "Odom GPS", which visualizes the GPS odometry. "gpsCovThreshold" can be adjusted to filter bad GPS readings. "poseCovThreshold" can be used to adjust the frequency of adding GPS factor to the graph. For example, you will notice the trajectory is constantly corrected by GPS whey you set "poseCovThreshold" to 1.0. Because of the heavy iSAM optimization, it's recommended that the playback speed is "-r 1".

<p align='center'>
    
</p>

  - **KITTI:** Since LIO-SAM needs a high-frequency IMU for function properly, we need to use KITTI raw data for testing. One problem remains unsolved is that the intrinsics of the IMU are unknown, which has a big impact on the accuracy of LIO-SAM. Download the provided sample data and make the following changes in "params.yaml":
    - extrinsicTrans: [-8.086759e-01, 3.195559e-01, -7.997231e-01]
    - extrinsicRot: [9.999976e-01, 7.553071e-04, -2.035826e-03, -7.854027e-04, 9.998898e-01, -1.482298e-02, 2.024406e-03, 1.482454e-02, 9.998881e-01]
    - extrinsicRPY: [9.999976e-01, 7.553071e-04, -2.035826e-03, -7.854027e-04, 9.998898e-01, -1.482298e-02, 2.024406e-03, 1.482454e-02, 9.998881e-01]
    - N_SCAN: 64
    - downsampleRate: 2 or 4
    - loopClosureEnableFlag: true or false

<p align='center'>
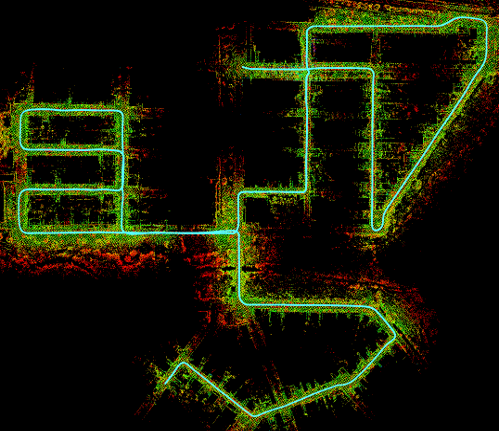
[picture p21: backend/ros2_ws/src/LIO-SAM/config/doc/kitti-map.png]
    
    
</p>

  - **Ouster lidar:** To make LIO-SAM work with Ouster lidar, some preparations needs to be done on hardware and software level.
    - Hardware:
      - Use an external IMU. LIO-SAM does not work with the internal 6-axis IMU of Ouster lidar. You need to attach a 9-axis IMU to the lidar and perform data-gathering.
      - Configure the driver. Change "timestamp_mode" in your Ouster launch file to "TIME_FROM_PTP_1588" so you can have ROS format timestamp for the point clouds.
    - Config:
      - Change "sensor" in "params.yaml" to "ouster".
      - Change "N_SCAN" and "Horizon_SCAN" in "params.yaml" according to your lidar, i.e., N_SCAN=128, Horizon_SCAN=1024.
    - Gen 1 and Gen 2 Ouster:
      It seems that the point coordinate definition might be different in different generations. Please refer to [Issue #94](https://github.com/TixiaoShan/LIO-SAM/issues/94) for debugging.

<p align='center'>
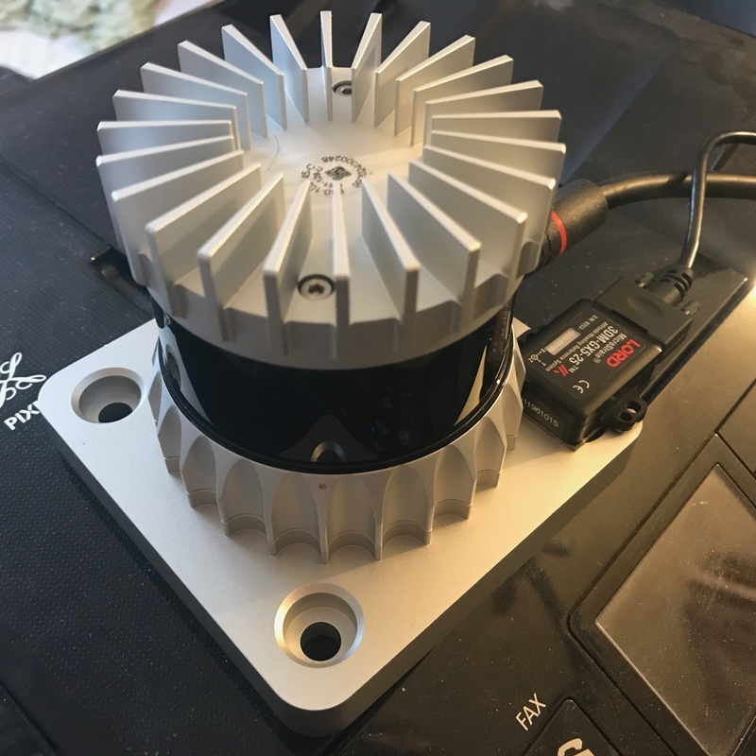
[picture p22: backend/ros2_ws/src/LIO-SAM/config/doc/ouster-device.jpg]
    
    
</p>

## Issues

  - **Zigzag or jerking behavior**: if your lidar and IMU data formats are consistent with the requirement of LIO-SAM, this problem is likely caused by un-synced timestamp of lidar and IMU data.

  - **Jumpping up and down**: if you start testing your bag file and the base_link starts to jump up and down immediately, it is likely your IMU extrinsics are wrong. For example, the gravity acceleration has negative value.

  - **mapOptimization crash**: it is usually caused by GTSAM. Please install the GTSAM specified in the README.md. More similar issues can be found [here](https://github.com/TixiaoShan/LIO-SAM/issues).

  - **gps odometry unavailable**: it is generally caused due to unavailable transform between message frame_ids and robot frame_id (for example: transform should be available from "imu_frame_id" and "gps_frame_id" to "base_link" frame. Please read the Robot Localization documentation found [here](http://docs.ros.org/en/melodic/api/robot_localization/html/preparing_sensor_data.html).

## Paper

Thank you for citing [LIO-SAM (IROS-2020)](./config/doc/paper.pdf) if you use any of this code.
```
@inproceedings{liosam2020shan,
  title={LIO-SAM: Tightly-coupled Lidar Inertial Odometry via Smoothing and Mapping},
  author={Shan, Tixiao and Englot, Brendan and Meyers, Drew and Wang, Wei and Ratti, Carlo and Rus Daniela},
  booktitle={IEEE/RSJ International Conference on Intelligent Robots and Systems (IROS)},
  pages={5135-5142},
  year={2020},
  organization={IEEE}
}
```

Part of the code is adapted from [LeGO-LOAM](https://github.com/RobustFieldAutonomyLab/LeGO-LOAM).
```
@inproceedings{legoloam2018shan,
  title={LeGO-LOAM: Lightweight and Ground-Optimized Lidar Odometry and Mapping on Variable Terrain},
  author={Shan, Tixiao and Englot, Brendan},
  booktitle={IEEE/RSJ International Conference on Intelligent Robots and Systems (IROS)},
  pages={4758-4765},
  year={2018},
  organization={IEEE}
}
```

## TODO

  - [ ] [Bug within imuPreintegration](https://github.com/TixiaoShan/LIO-SAM/issues/104)

## Related Package

  - [Lidar-IMU calibration](https://github.com/chennuo0125-HIT/lidar_imu_calib)
  - [LIO-SAM with Scan Context](https://github.com/gisbi-kim/SC-LIO-SAM)

## Acknowledgement

  - LIO-SAM is based on LOAM (J. Zhang and S. Singh. LOAM: Lidar Odometry and Mapping in Real-time).

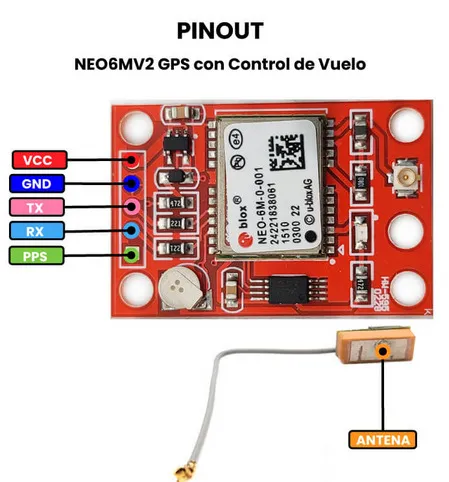
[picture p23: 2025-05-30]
assets/images/wiring/gps_neo-6m_pinout.webp

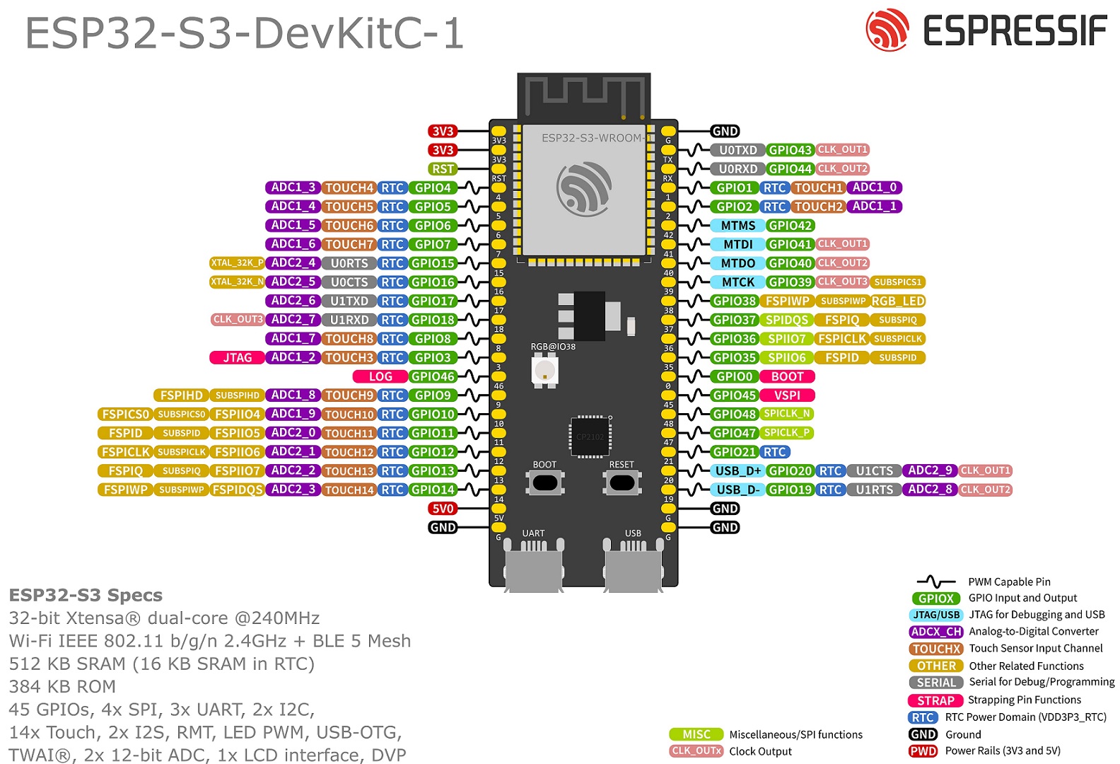
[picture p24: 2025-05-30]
assets/images/wiring/esp32-s3_pinout.jpg

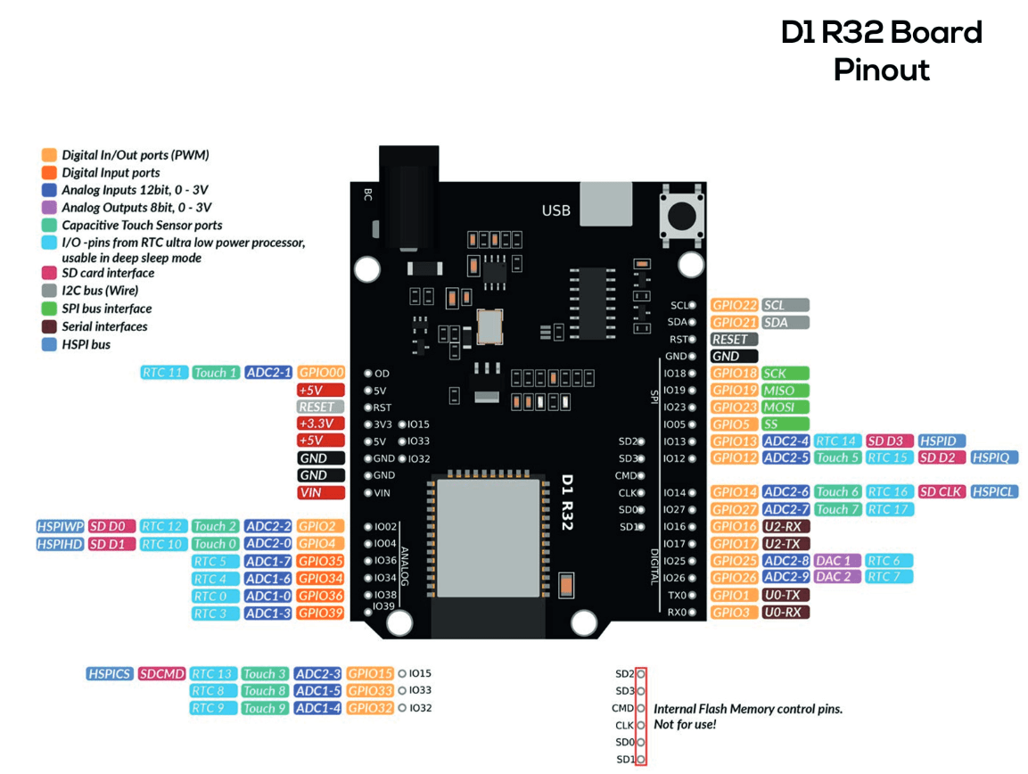
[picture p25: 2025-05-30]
assets/images/wiring/wemos_d1-r32_pinout.png

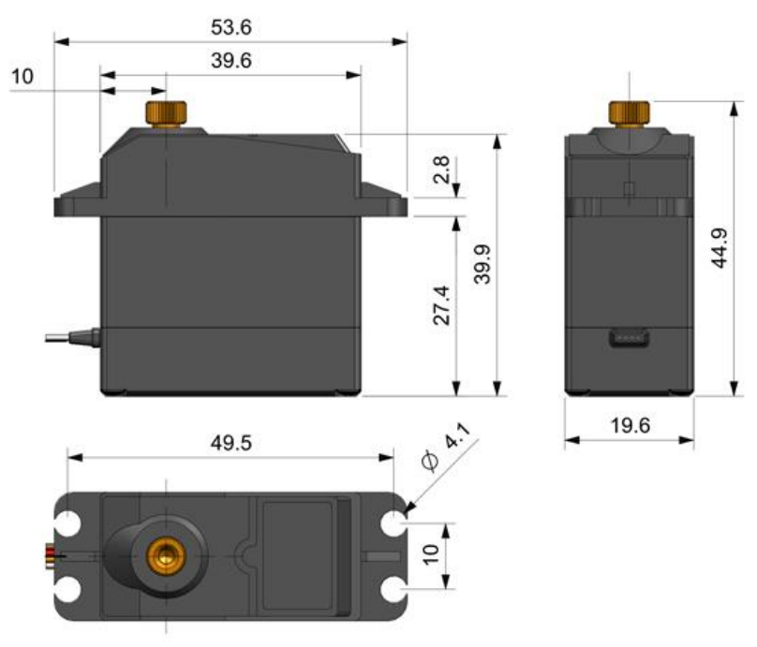
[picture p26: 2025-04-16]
design/3d_files/tilting_lidar_mount/dimensions/servo_dms15.PNG

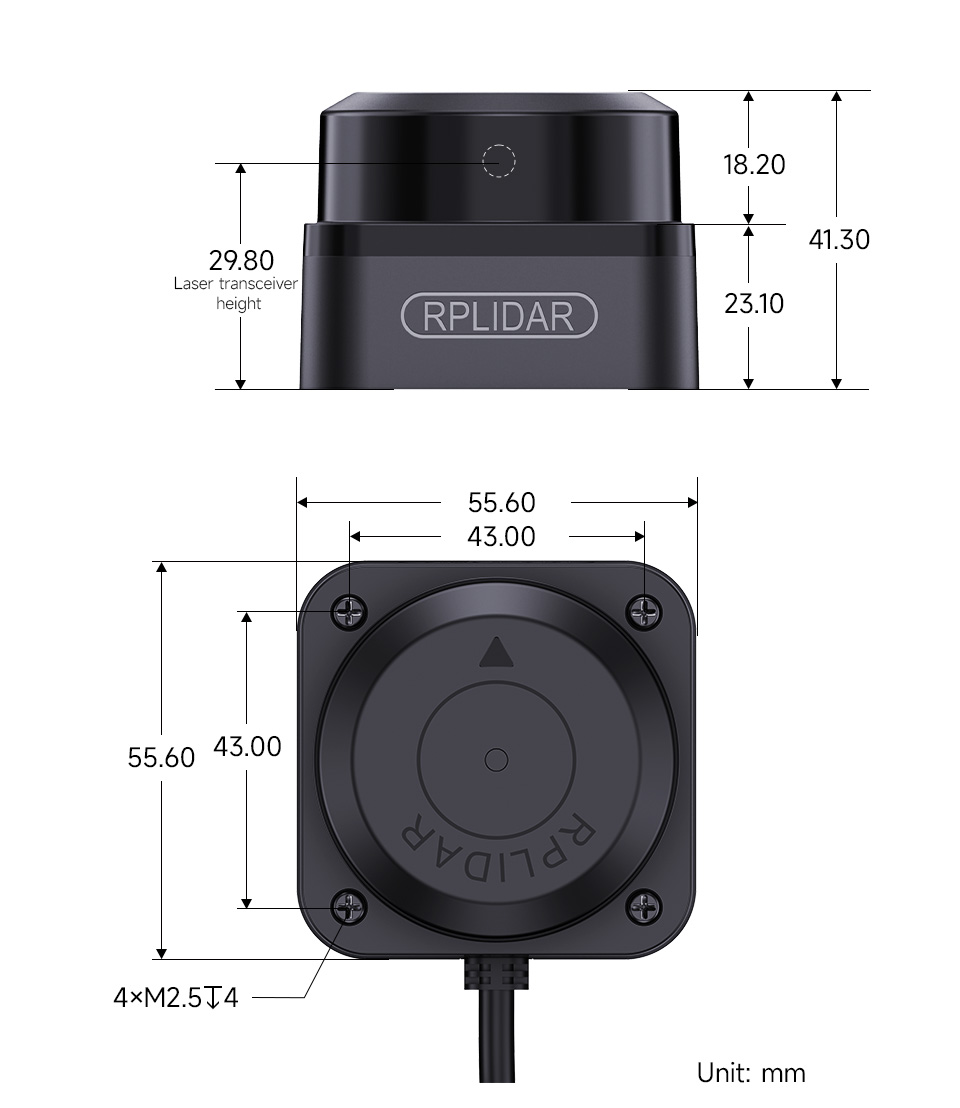
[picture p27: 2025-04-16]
design/3d_files/tilting_lidar_mount/dimensions/rplidar_c1.jpg

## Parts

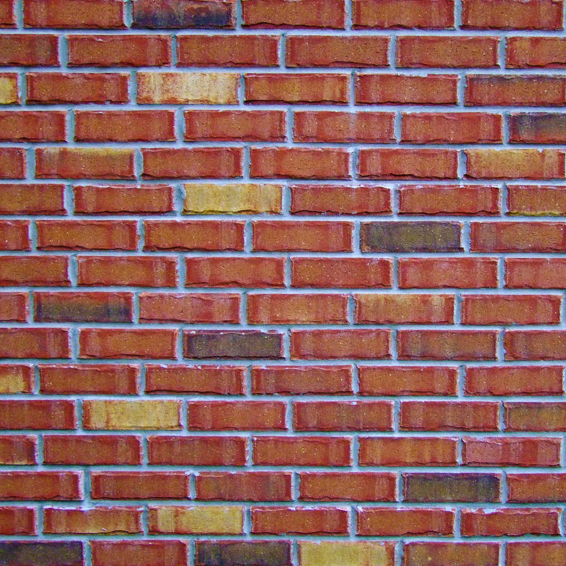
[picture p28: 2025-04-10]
backend/models/brick_box_3x1x3/materials/textures/simple_box.png

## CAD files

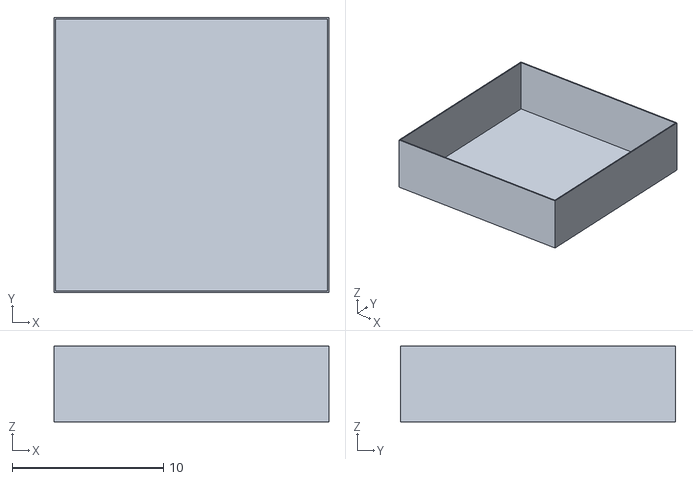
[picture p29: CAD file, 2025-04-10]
backend/models/rtab_map_stage/meshes/rtab_map_stage.stl
18.2 x 18.2 x 5.00

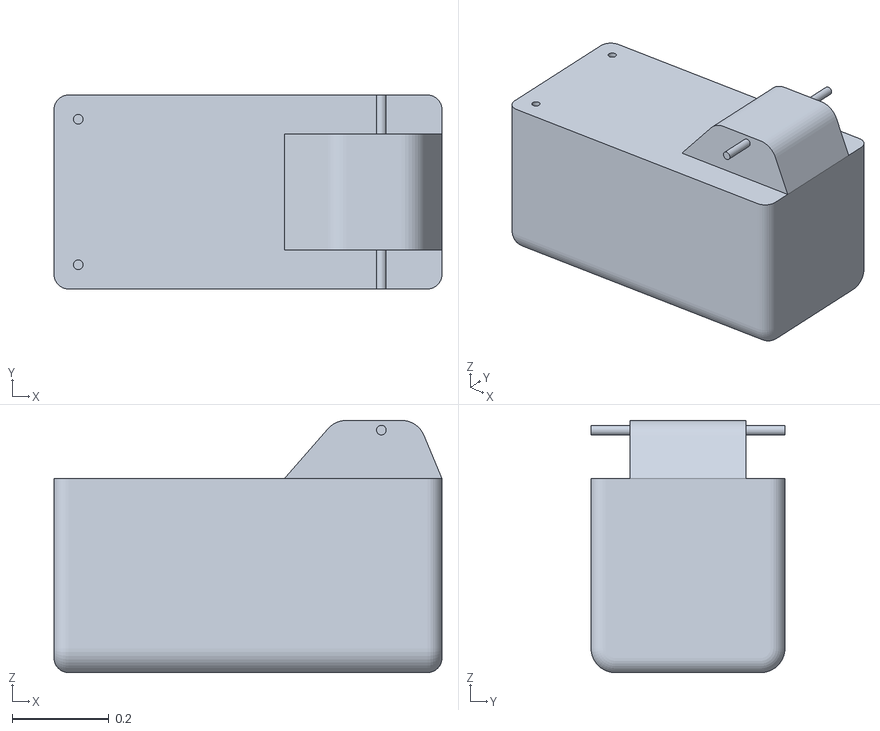
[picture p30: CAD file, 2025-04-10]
backend/ros2_ws/src/robot_description/meshes/STL/base/base_link.stl
0.8 x 0.4 x 0.52

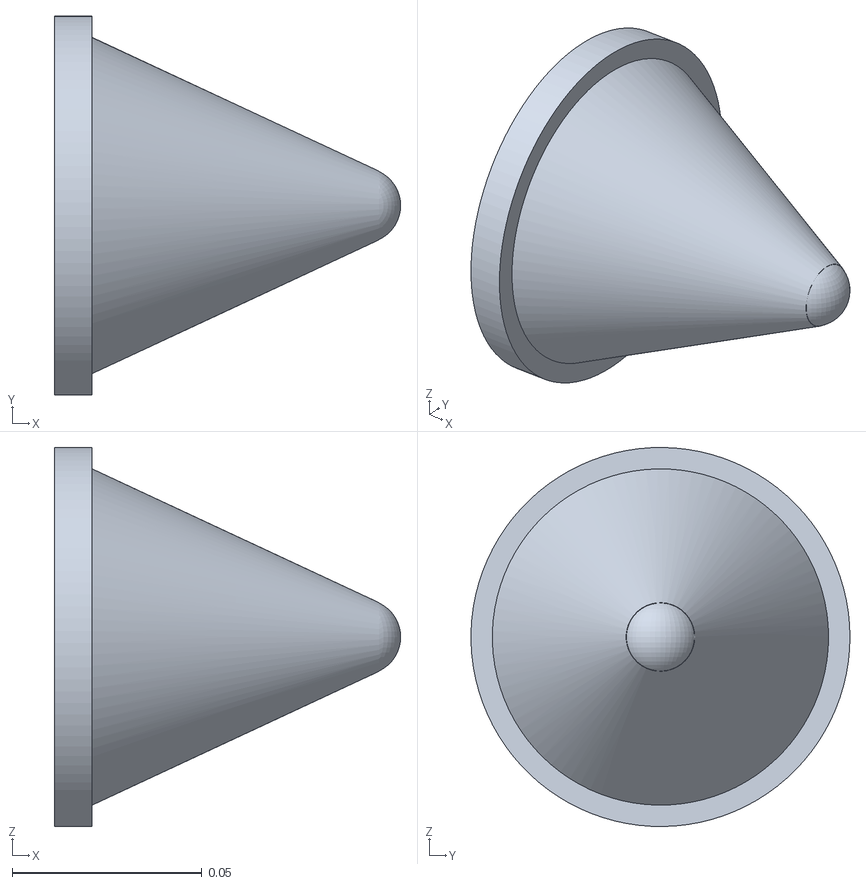
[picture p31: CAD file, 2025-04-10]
backend/ros2_ws/src/robot_description/meshes/STL/camera/camera.stl
0.0914 x 0.1 x 0.1

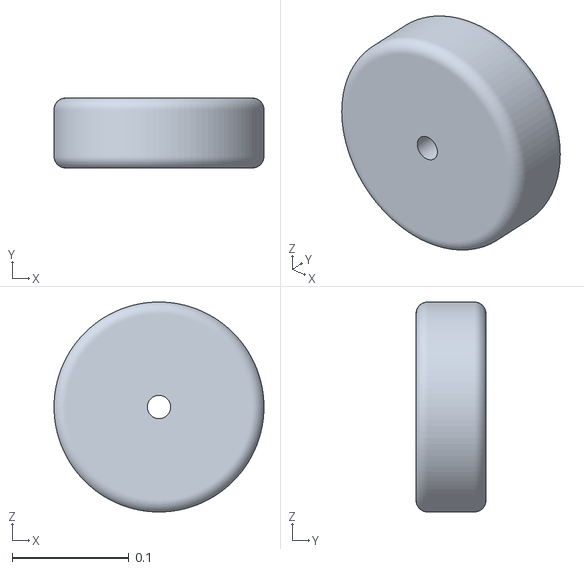
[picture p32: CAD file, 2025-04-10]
backend/ros2_ws/src/robot_description/meshes/STL/front_wheel/wheel.stl
0.18 x 0.06 x 0.18

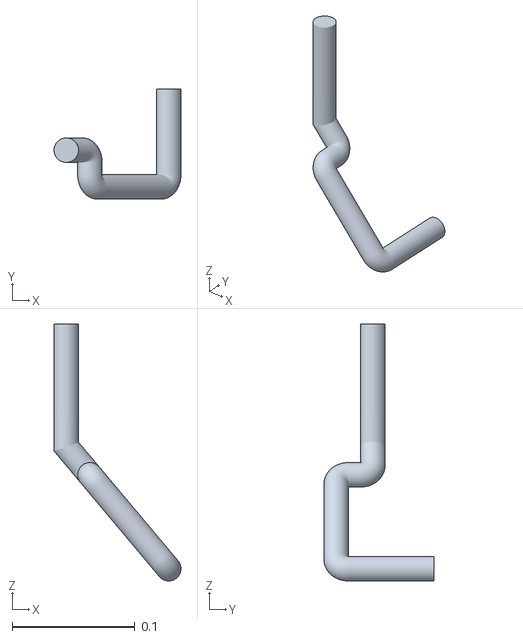
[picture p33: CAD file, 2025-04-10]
backend/ros2_ws/src/robot_description/meshes/STL/suspension/front_right_sus.stl
0.104 x 0.09 x 0.21

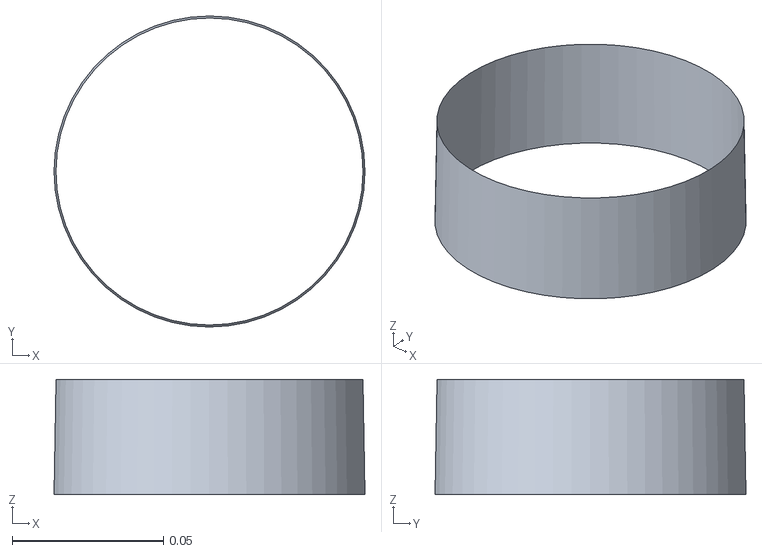
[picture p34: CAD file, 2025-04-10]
backend/ros2_ws/src/robot_gazebo/models/velodyne_description/meshes/VLP16_scan.stl
0.103 x 0.103 x 0.0381

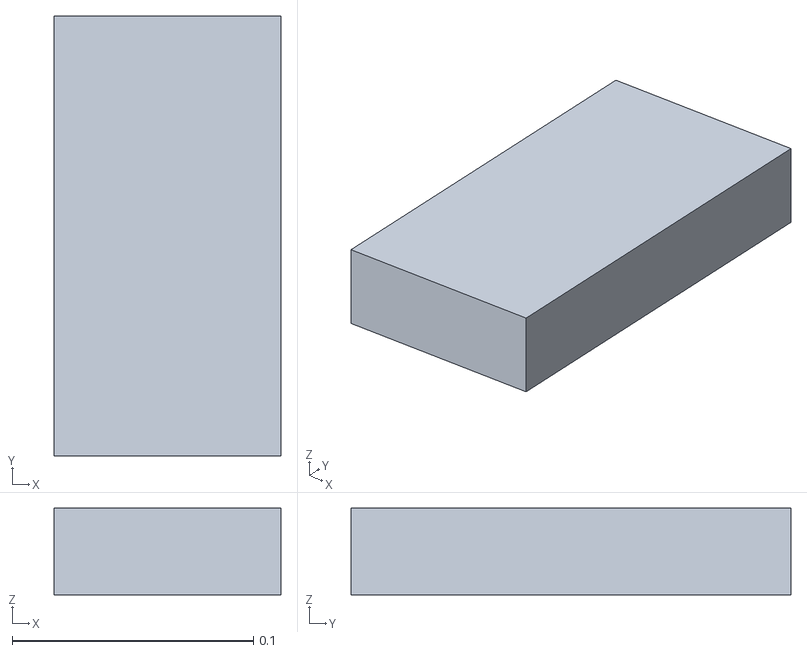
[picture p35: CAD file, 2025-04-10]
backend/ros2_ws/src/robot_gazebo/models/velodyne_description/models/rs_robot/meshes/STL/base/base_link.stl
0.094 x 0.182 x 0.036

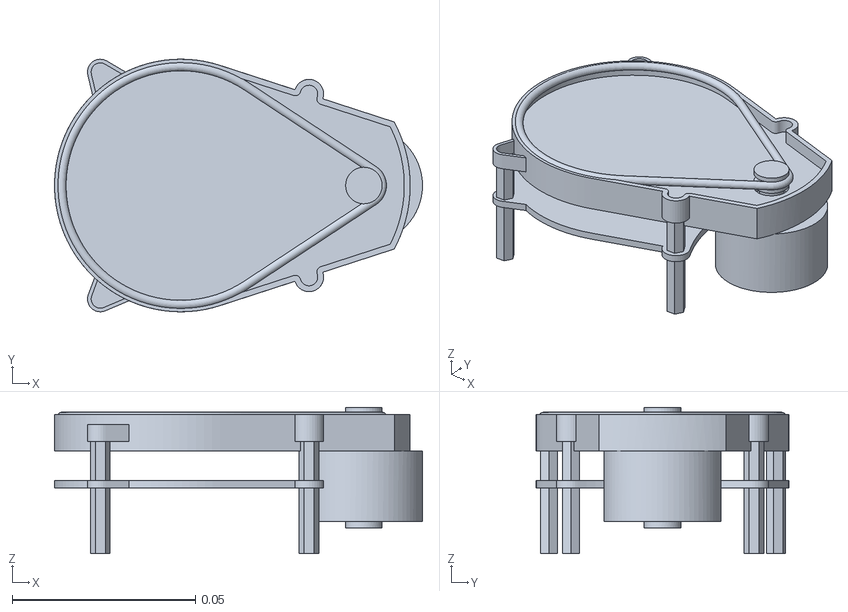
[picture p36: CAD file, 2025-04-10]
backend/ros2_ws/src/robot_gazebo/models/velodyne_description/models/rs_robot/meshes/STL/lidar_base/YDlidar_base.stl
0.101 x 0.069 x 0.04

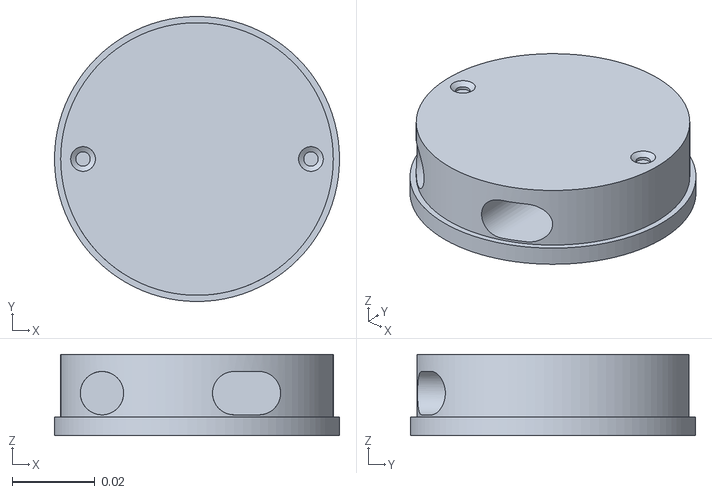
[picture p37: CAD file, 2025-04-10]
backend/ros2_ws/src/robot_gazebo/models/velodyne_description/models/rs_robot/meshes/STL/lidar_head/YDlidar_head v4.stl
0.069 x 0.069 x 0.0197

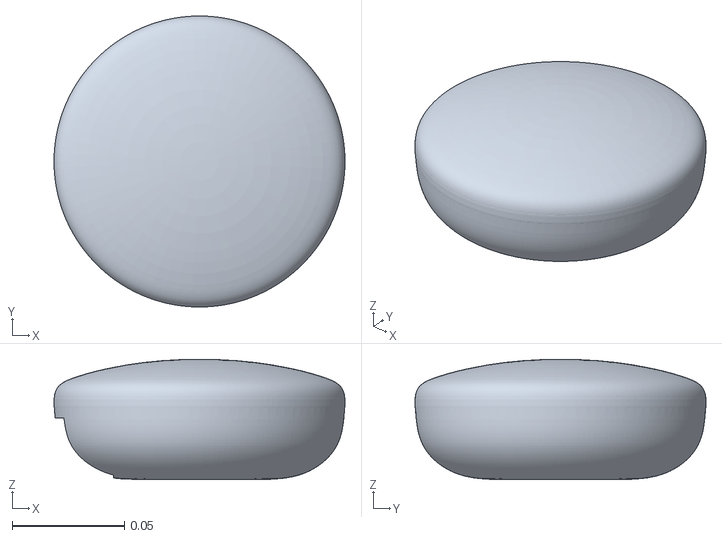
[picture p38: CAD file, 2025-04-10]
backend/ros2_ws/src/robot_gazebo/models/velodyne_description/models/rs_robot/meshes/STL/sensors/gps/gps.stl
0.13 x 0.13 x 0.0536

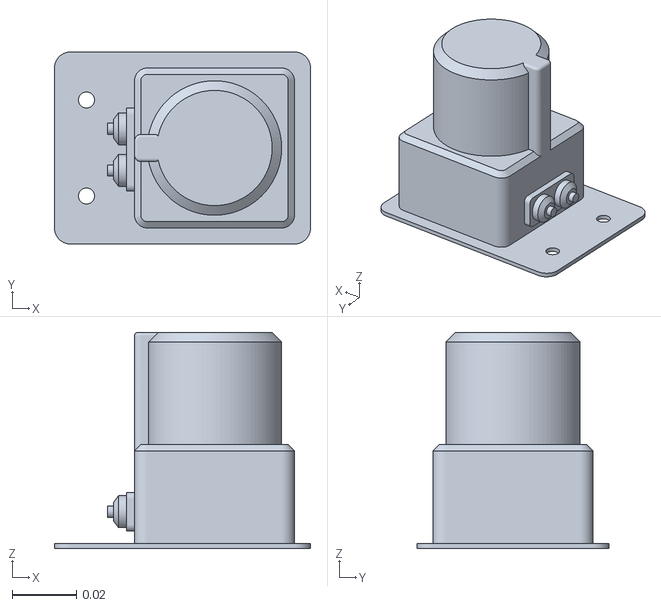
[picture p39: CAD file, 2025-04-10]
backend/ros2_ws/src/robot_gazebo/models/velodyne_description/models/rs_robot/meshes/STL/sensors/rear_lrf/rear_lrf.stl
0.08 x 0.06 x 0.0675

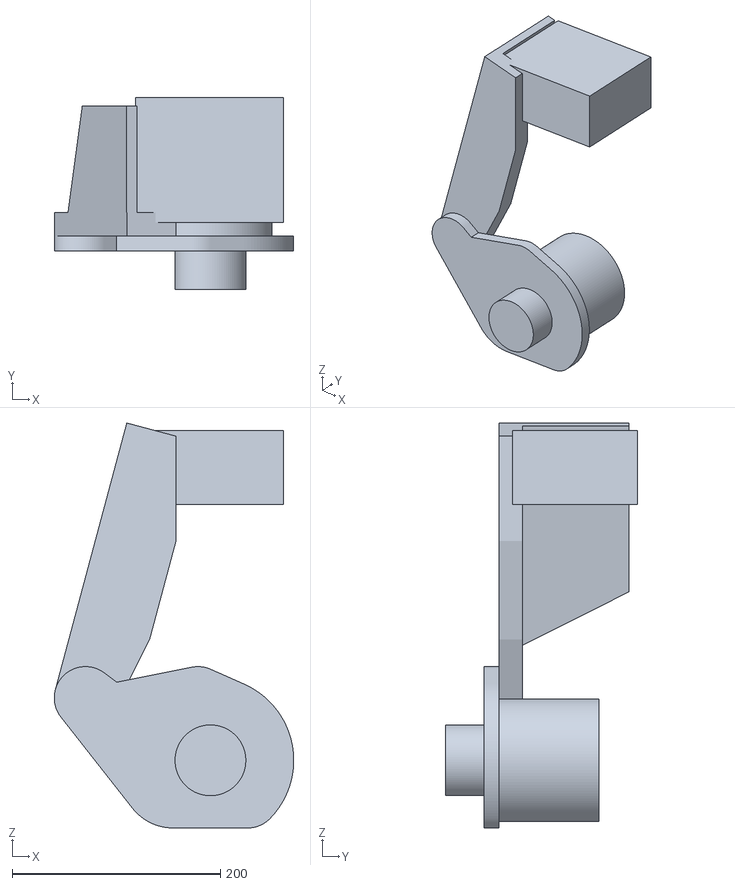
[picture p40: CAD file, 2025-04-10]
backend/ros2_ws/src/robot_gazebo/models/velodyne_description/models/rs_robot/meshes/STL/suspension/FRONT_LEFT_LINKSTL.stl
230.0 x 184.0 x 388.9

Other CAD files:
backend/ros2_ws/src/robot_description/meshes/STL/suspension/front_left_sus.stl
backend/ros2_ws/src/robot_gazebo/models/robot/meshes/STL/suspension/front_left_sus.stl
backend/ros2_ws/src/robot_gazebo/models/velodyne_description/meshes/HDL32E_base.stl
backend/ros2_ws/src/robot_gazebo/models/velodyne_description/meshes/HDL32E_scan.stl
backend/ros2_ws/src/robot_gazebo/models/velodyne_description/meshes/VLP16_base_1.stl
backend/ros2_ws/src/robot_gazebo/models/velodyne_description/meshes/VLP16_base_2.stl
backend/ros2_ws/src/robot_gazebo/models/velodyne_description/models/rs_robot/meshes/STL/base/base_link_old.stl
backend/ros2_ws/src/robot_gazebo/models/velodyne_description/models/rs_robot/meshes/STL/suspension/FRONT_RIGHT_LINKSTL.stl
backend/ros2_ws/src/robot_gazebo/models/velodyne_description/models/rs_robot/meshes/STL/suspension/REAR_LEFT_LINKSTL.stl
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

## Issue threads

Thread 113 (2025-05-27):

Add the second esp32 to the physical circuit

Nocksem, 2025-05-27:
Since we decided to use a second esp32, we need to wire it to the circuit. This can be done using the following diagram of what the circuit should be at the end:

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

Closed 2025-05-30.

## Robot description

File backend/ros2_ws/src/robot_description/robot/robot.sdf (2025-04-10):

<sdf version='1.7'>
  <model name='yn_robot'>

    <link name="base_footprint"/>

    <link name='base_link'>
      <inertial>
        <pose>0 0 -0.033898 0 -0 0</pose>
        <mass>10.845</mass>
        <inertia>
          <ixx>0.385476</ixx>
          <ixy>1.25563e-36</ixy>
          <ixz>1.45924e-18</ixz>
          <iyy>0.355476</iyy>
          <iyz>-0.035</iyz>
          <izz>0.352105</izz>
        </inertia>
      </inertial>
      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
      <self_collide>0</self_collide>
      <gravity>1</gravity>
      <sensor name='imu_sensor' type='imu'>
        <always_on>1</always_on>
        <update_rate>200</update_rate>
        <visualize>1</visualize>
        <topic>__default_topic__</topic>
        <plugin name='imu_plugin' filename='libgazebo_ros_imu_sensor.so'>
          <topicName>imu_raw</topicName>
          <update_rate>0</update_rate>
          <bodyName>imu_link</bodyName>
          <updateRateHZ>200.0</updateRateHZ>
          <gaussianNoise>0.0</gaussianNoise>
          <xyzOffset>0 0 0</xyzOffset>
          <rpyOffset>0 0 0</rpyOffset>
          <frameName>base_link</frameName>
          <initialOrientationAsReference>0</initialOrientationAsReference>
        </plugin>
        <pose>0 0 -0.297322 3.14159 0 3.14159</pose>
      </sensor>
      <sensor name='velodyne-VLP16' type='ray'>
        <visualize>0</visualize>
        <update_rate>10</update_rate>
        <ray>
          <scan>
            <horizontal>
              <samples>440</samples>
              <resolution>1</resolution>
              <min_angle>-3.14159</min_angle>
              <max_angle>3.14159</max_angle>
            </horizontal>
            <vertical>
              <samples>16</samples>
              <resolution>1</resolution>
              <min_angle>-0.261799</min_angle>
              <max_angle>0.261799</max_angle>
            </vertical>
          </scan>
          <range>
            <min>0.3</min>
            <max>131</max>
            <resolution>0.001</resolution>
          </range>
          <noise>
            <type>gaussian</type>
            <mean>0</mean>
            <stddev>0</stddev>
          </noise>
        </ray>
        <plugin name='gazebo_ros_laser_controller' filename='libgazebo_ros_velodyne_laser.so'>
          <topicName>/points_raw</topicName>
          <frameName>velodyne</frameName>
          <min_range>0.9</min_range>
          <max_range>130.0</max_range>
          <gaussianNoise>0.008</gaussianNoise>
        </plugin>
        <pose>0 0 -0.4377 3.14159 0 3.14159</pose>
      </sensor>
    </link>
    <joint name='front_left_steering_joint' type='revolute'>
      <pose relative_to='base_link'>-0.35 0.15 0 3.14159 -0 0</pose>
      <parent>base_link</parent>
      <child>front_left_steering_link</child>
      <axis>
        <xyz>0 0 1</xyz>
        <limit>
          <lower>-2.1</lower>
          <upper>2.1</upper>
          <effort>5</effort>
          <velocity>6.28</velocity>
        </limit>
        <dynamics>
          <spring_reference>0</spring_reference>
          <spring_stiffness>0</spring_stiffness>
        </dynamics>
      </axis>
    </joint>
    <link name='front_left_steering_link'>
      <pose relative_to='front_left_steering_joint'>0 0 0 0 -0 0</pose>
      <inertial>
        <pose>0 0 -0.02 0 -0 0</pose>
        <mass>0.15</mass>
        <inertia>
          <ixx>1e-05</ixx>
          <ixy>0</ixy>
          <ixz>0</ixz>
          <iyy>1e-05</iyy>
          <iyz>0</iyz>
          <izz>4e-06</izz>
        </inertia>
      </inertial>
      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
      <self_collide>0</self_collide>
    </link>
    <joint name='front_left_wheel_joint' type='revolute'>
      <pose relative_to='front_left_steering_link'>0.083562 -0.02 -0.099586 0 -0 0</pose>
      <parent>front_left_steering_link</parent>
      <child>front_left_wheel_link</child>
      <axis>
        <xyz>0 -1 0</xyz>
        <limit>
          <effort>1.5</effort>
          <velocity>20</velocity>
          <lower>-1e+16</lower>
          <upper>1e+16</upper>
        </limit>
        <dynamics>
          <spring_reference>0</spring_reference>
          <spring_stiffness>0</spring_stiffness>
        </dynamics>
      </axis>
    </joint>
    <link name='front_left_wheel_link'>
      <pose relative_to='front_left_wheel_joint'>0 0 0 0 -0 0</pose>
      <inertial>
        <pose>0 0 0 0 -0 0</pose>
        <mass>0.137</mass>
        <inertia>
          <ixx>6e-05</ixx>
          <ixy>0</ixy>
          <ixz>0</ixz>
          <iyy>0.00011</iyy>
          <iyz>0</iyz>
          <izz>6e-05</izz>
        </inertia>
      </inertial>
      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
      <self_collide>0</self_collide>
    </link>
    <joint name='front_right_steering_joint' type='revolute'>
      <pose relative_to='base_link'>-0.35 -0.15 0 3.14159 -0 0</pose>
      <parent>base_link</parent>
      <child>front_right_steering_link</child>
      <axis>
        <xyz>0 0 1</xyz>
        <limit>
          <lower>-2.1</lower>
          <upper>2.1</upper>
          <effort>5</effort>
          <velocity>6.28</velocity>
        </limit>
        <dynamics>
          <spring_reference>0</spring_reference>
          <spring_stiffness>0</spring_stiffness>
        </dynamics>
      </axis>
    </joint>
    <link name='front_right_steering_link'>
      <pose relative_to='front_right_steering_joint'>0 0 0 0 -0 0</pose>
      <inertial>
        <pose>0 0 -0.02 0 -0 0</pose>
        <mass>0.15</mass>
        <inertia>
          <ixx>1e-05</ixx>
          <ixy>0</ixy>
          <ixz>0</ixz>
          <iyy>1e-05</iyy>
          <iyz>0</iyz>
          <izz>4e-06</izz>
        </inertia>
      </inertial>
      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
      <self_collide>0</self_collide>
    </link>
    <joint name='front_right_wheel_joint' type='revolute'>
      <pose relative_to='front_right_steering_link'>0.083562 0.02 -0.099586 0 -0 0</pose>
      <parent>front_right_steering_link</parent>
      <child>front_right_wheel_link</child>
      <axis>
        <xyz>0 1 0</xyz>
        <limit>
          <effort>1.5</effort>
          <velocity>20</velocity>
          <lower>-1e+16</lower>
          <upper>1e+16</upper>
        </limit>
        <dynamics>
          <spring_reference>0</spring_reference>
          <spring_stiffness>0</spring_stiffness>
        </dynamics>
      </axis>
    </joint>
    <link name='front_right_wheel_link'>
      <pose relative_to='front_right_wheel_joint'>0 0 0 0 -0 0</pose>
      <inertial>
        <pose>0 0 0 0 -0 0</pose>
        <mass>0.137</mass>
        <inertia>
          <ixx>6e-05</ixx>
          <ixy>0</ixy>
          <ixz>0</ixz>
          <iyy>0.00011</iyy>
          <iyz>0</iyz>
          <izz>6e-05</izz>
        </inertia>
      </inertial>
      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
      <self_collide>0</self_collide>
    </link>
    <joint name='left_wheel_joint' type='revolute'>
      <pose relative_to='base_link'>0.275 0.17 0.1 0 -0 3.14159</pose>
      <parent>base_link</parent>
      <child>left_wheel_link</child>
      <axis>
        <xyz>0 -1 0</xyz>
        <limit>
          <lower>-1e+16</lower>
          <upper>1e+16</upper>
        </limit>
        <dynamics>
          <spring_reference>0</spring_reference>
          <spring_stiffness>0</spring_stiffness>
        </dynamics>
      </axis>
    </joint>
    <link name='left_wheel_link'>
      <pose relative_to='left_wheel_joint'>0 0 0 0 -0 0</pose>
      <inertial>
        <pose>0 0 0 0 -0 0</pose>
        <mass>1.75</mass>
        <inertia>
          <ixx>0.00458</ixx>
          <ixy>0</ixy>
          <ixz>0</ixz>
          <iyy>0.00871</iyy>
          <iyz>0</iyz>
          <izz>0.00458</izz>
        </inertia>
      </inertial>
      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
      <self_collide>0</self_collide>
    </link>
    <joint name='right_wheel_joint' type='revolute'>
      <pose relative_to='base_link'>0.275 -0.17 0.1 0 -0 0</pose>
      <parent>base_link</parent>
      <child>right_wheel_link</child>
      <axis>
        <xyz>0 1 0</xyz>
        <limit>
          <lower>-1e+16</lower>
          <upper>1e+16</upper>
        </limit>
        <dynamics>
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

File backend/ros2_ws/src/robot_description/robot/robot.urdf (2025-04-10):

<?xml version="1.0" ?>
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
<robot name="yn_robot">
  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
  <link name="base_footprint"/>
  <joint name="footprint" type="fixed">
    <origin rpy="0 0 0" xyz="0 0 0"/>
    <parent link="base_footprint"/>
    <child link="base_link"/>
  </joint>
  <link name="base_link">
    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
    <inertial>
      <origin xyz="0 0 0"/>
      <mass value="10"/>
      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
    </inertial>
  </link>
  <joint name="front_right_steering_joint" type="revolute">
    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
    <origin rpy="3.141592653589793 0 0" xyz="-0.35 -0.15 0"/>
    <parent link="base_link"/>
    <child link="front_right_steering_link"/>
    <limit effort="5" lower="-2.1" upper="2.1" velocity="6.28"/>
    <axis xyz="0 0 1"/>
  </joint>
  <link name="front_right_steering_link">
    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
    <inertial>
      <origin xyz="0 0 -0.02"/>
      <mass value="0.15"/>
      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
    </inertial>
  </link>
  <joint name="front_left_steering_joint" type="revolute">
    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
    <origin rpy="3.141592653589793 0 0" xyz="-0.35 0.15 0"/>
    <parent link="base_link"/>
    <child link="front_left_steering_link"/>
    <limit effort="5" lower="-2.1" upper="2.1" velocity="6.28"/>
    <axis xyz="0 0 1"/>
  </joint>
  <link name="front_left_steering_link">
    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
    <inertial>
      <origin xyz="0 0 -0.02"/>
      <mass value="0.15"/>
      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
    </inertial>
  </link>
  <joint name="front_right_wheel_joint" type="continuous">
    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
    <origin xyz="0.083562 0.02 -0.099586"/>
    <parent link="front_right_steering_link"/>
    <child link="front_right_wheel_link"/>
    <limit effort="1.5" velocity="20"/>
    <axis xyz="0 1 0"/>
  </joint>
  <link name="front_right_wheel_link">
    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
    <inertial>
      <origin xyz="0 0 0"/>
      <mass value="0.137"/>
      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
    </inertial>
  </link>
  <joint name="front_left_wheel_joint" type="continuous">
    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
    <origin xyz="0.083562 -0.02 -0.099586"/>
    <parent link="front_left_steering_link"/>
    <child link="front_left_wheel_link"/>
    <limit effort="1.5" velocity="20"/>
    <axis xyz="0 -1 0"/>
  </joint>
  <link name="front_left_wheel_link">
    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
    <inertial>
      <origin xyz="0 0 0"/>
      <mass value="0.137"/>
      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
    </inertial>
  </link>
  <joint name="right_wheel_joint" type="continuous">
    <origin rpy="0 0 0" xyz="0.275 -0.17 0.1"/>
    <parent link="base_link"/>
    <child link="right_wheel_link"/>
    <axis xyz="0 1 0"/>
  </joint>
  <link name="right_wheel_link">
    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
    <inertial>
      <origin xyz="0 0 0"/>
      <mass value="1.75"/>
      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
    </inertial>
  </link>
  <joint name="left_wheel_joint" type="continuous">
    <origin rpy="0 0 3.141592653589793" xyz="0.275 0.17 0.1"/>
    <parent link="base_link"/>
    <child link="left_wheel_link"/>
    <axis xyz="0 -1 0"/>
  </joint>
  <link name="left_wheel_link">
    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
    <inertial>
      <origin xyz="0 0 0"/>
      <mass value="1.75"/>
      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
    </inertial>
  </link>
  <joint name="velodyne_base_mount_joint" type="fixed">
    <origin rpy="0 3.141592653589793 0" xyz="0 0 -0.4"/>
    <parent link="base_link"/>
    <child link="velodyne_base_link"/>
  </joint>
  <link name="velodyne_base_link">
    <inertial>
      <mass value="0.83"/>
      <origin xyz="0 0 0.03585"/>
      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
    </inertial>
    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
  </link>
  <joint name="velodyne_base_scan_joint" type="fixed">
    <origin rpy="0 0 0" xyz="0 0 0.0377"/>
    <parent link="velodyne_base_link"/>
    <child link="velodyne"/>
  </joint>
  <link name="velodyne">
    <inertial>
      <mass value="0.01"/>
      <origin xyz="0 0 0"/>
      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
    </inertial>
    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
  </link>
  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
  <joint name="imu_joint" type="fixed">
    <origin rpy="0 3.141592653589793 0" xyz="0 0 -0.297322"/>
    <parent link="base_link"/>
    <child link="imu_link"/>
  </joint>
  <link name="imu_link">
    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
    <inertial>
      <origin xyz="0 0 0"/>
      <mass value="0.005"/>
      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
    </inertial>
  </link>
  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
</robot>

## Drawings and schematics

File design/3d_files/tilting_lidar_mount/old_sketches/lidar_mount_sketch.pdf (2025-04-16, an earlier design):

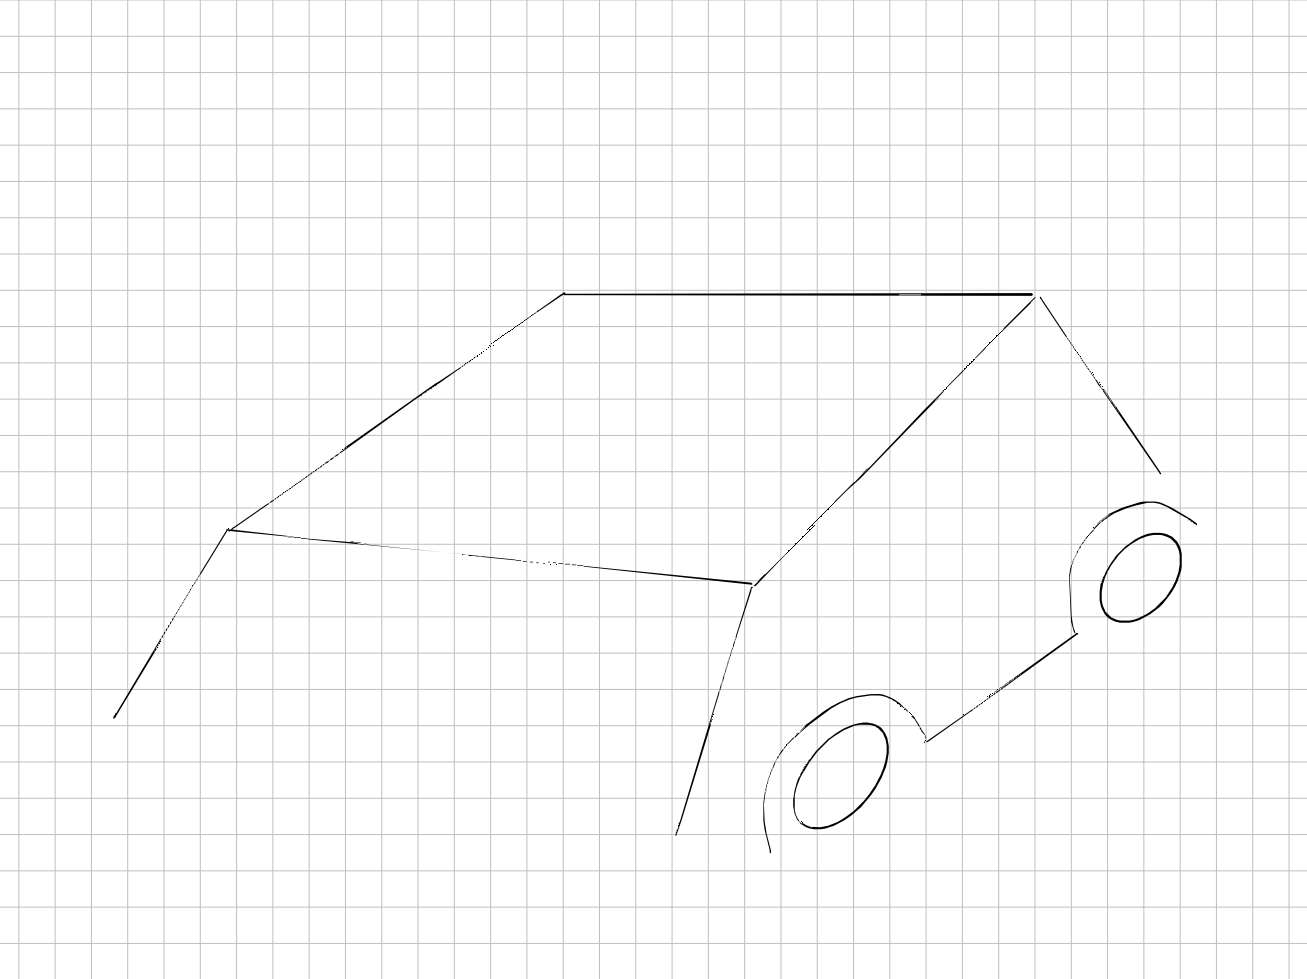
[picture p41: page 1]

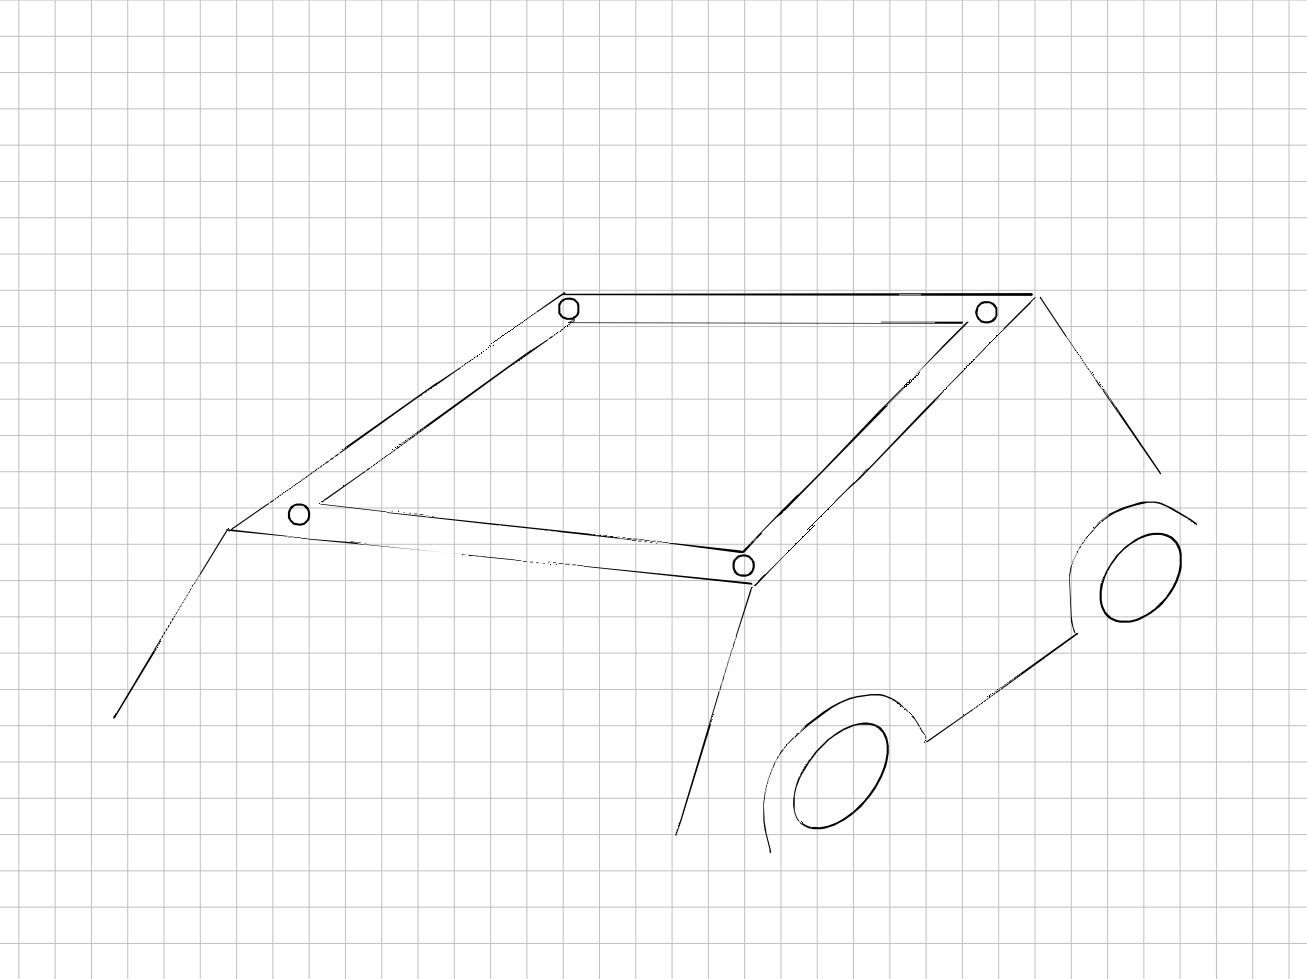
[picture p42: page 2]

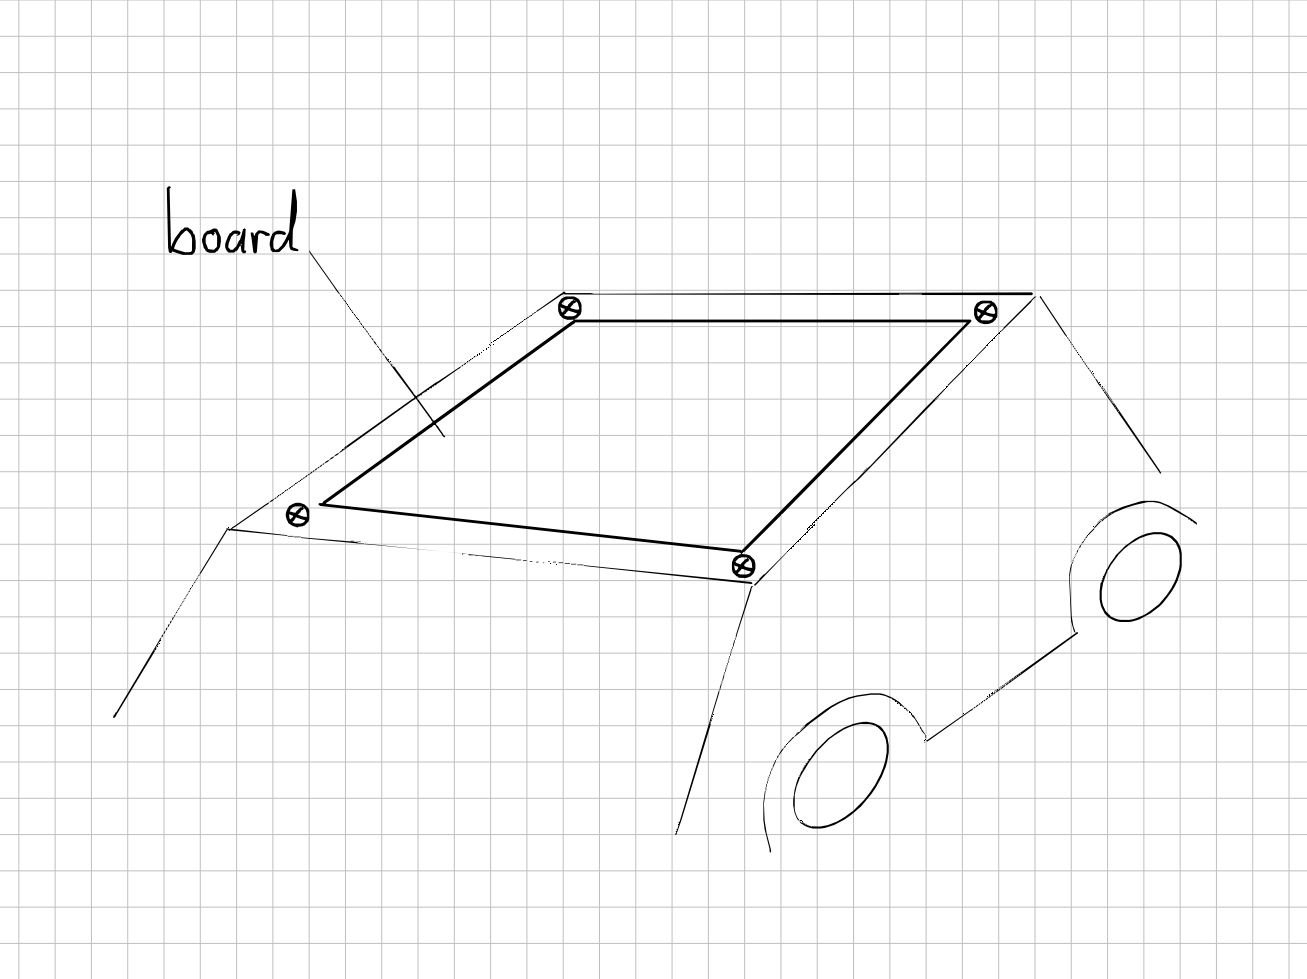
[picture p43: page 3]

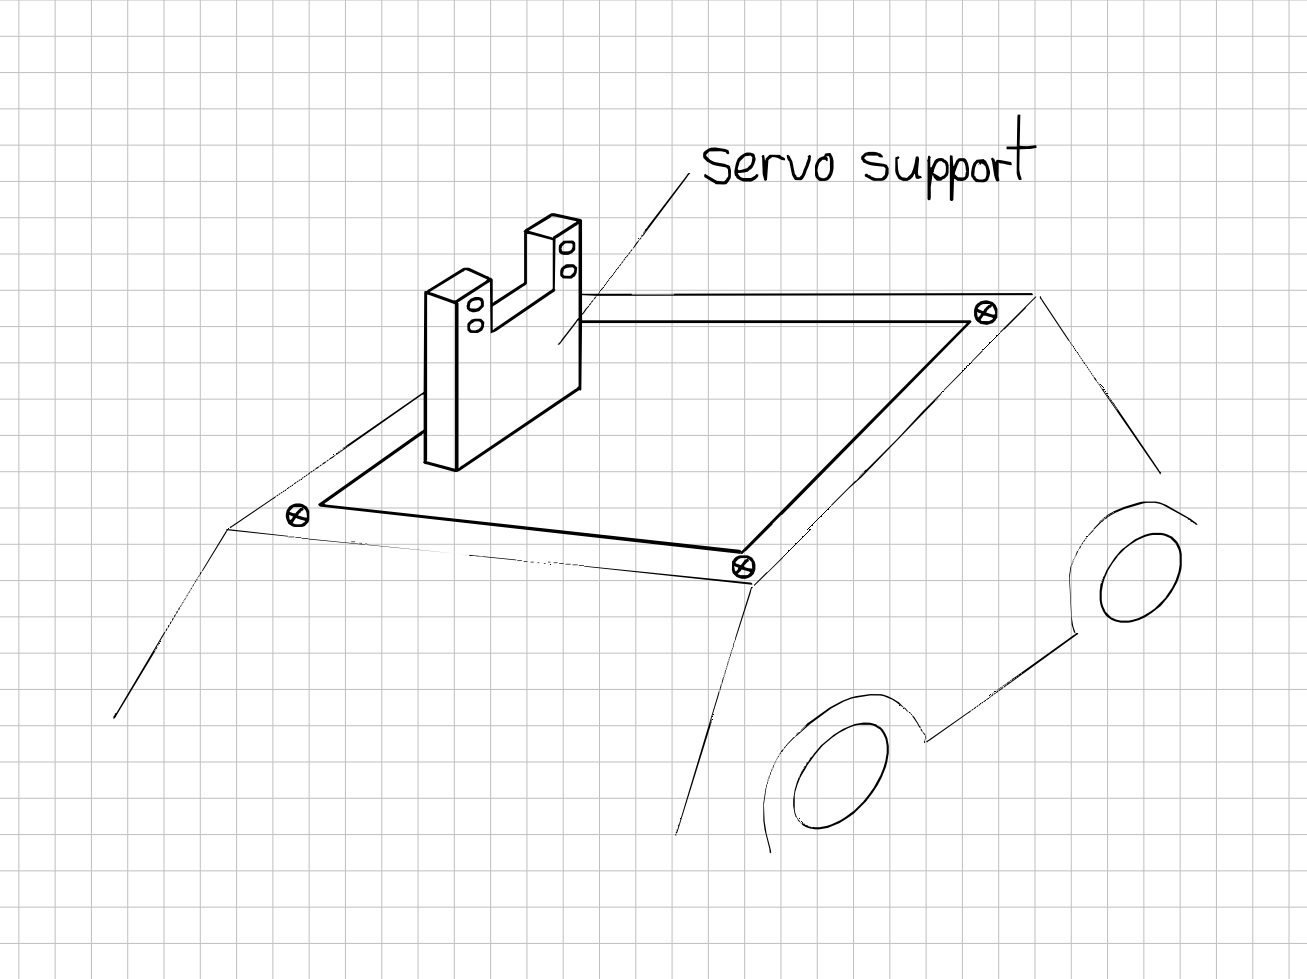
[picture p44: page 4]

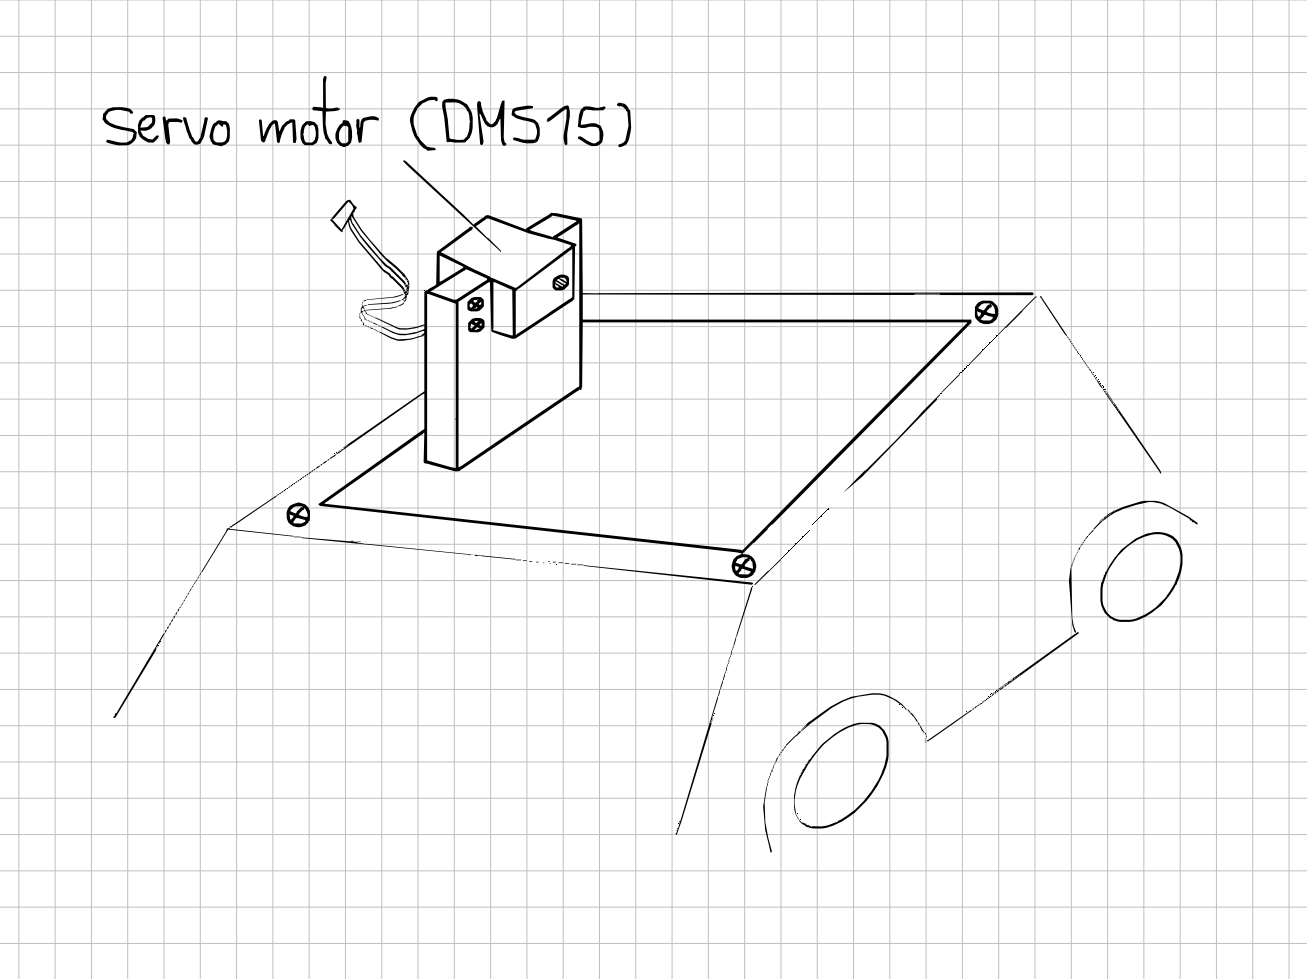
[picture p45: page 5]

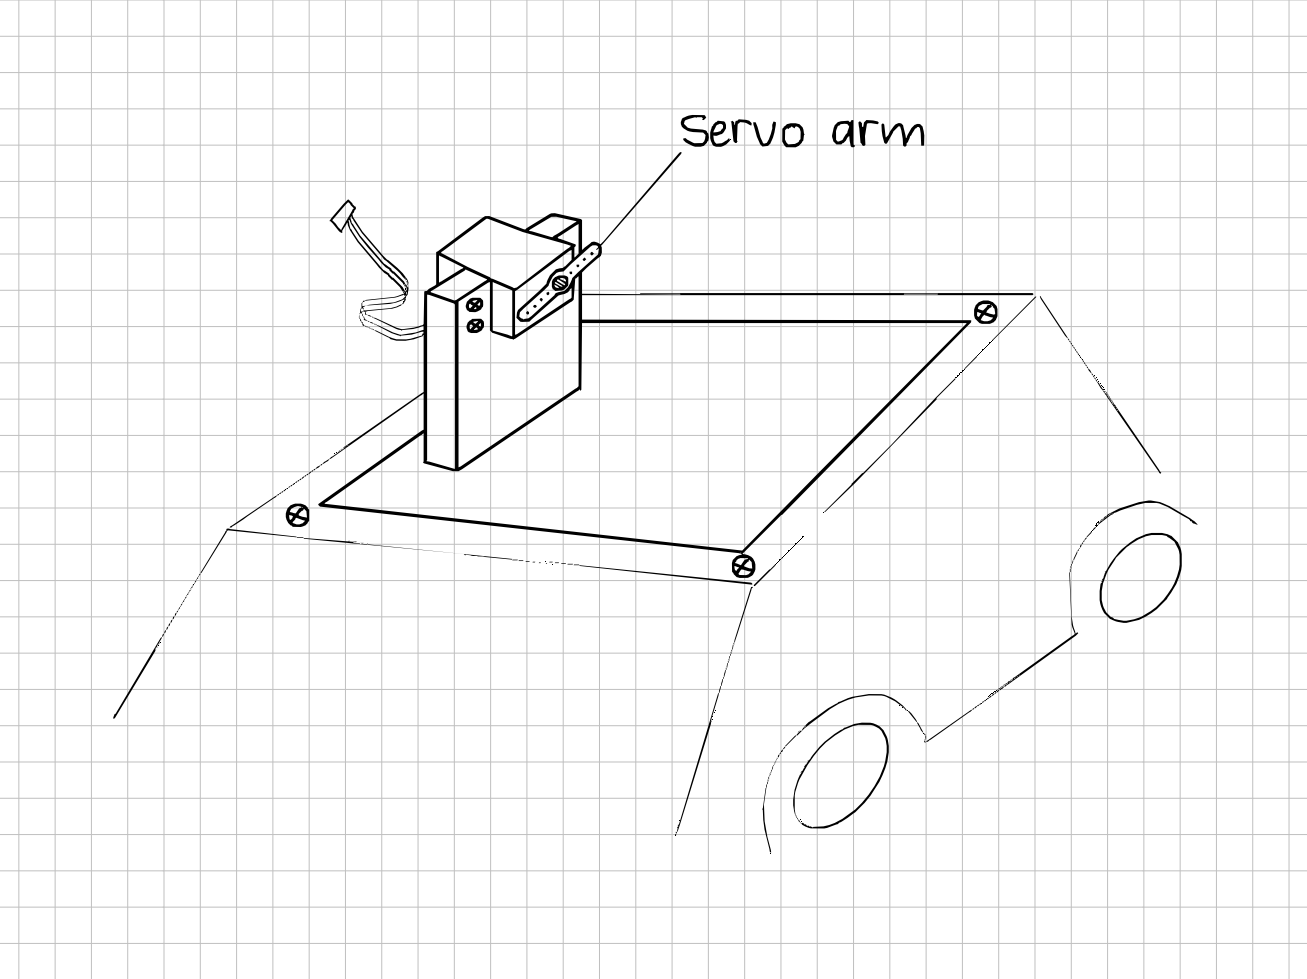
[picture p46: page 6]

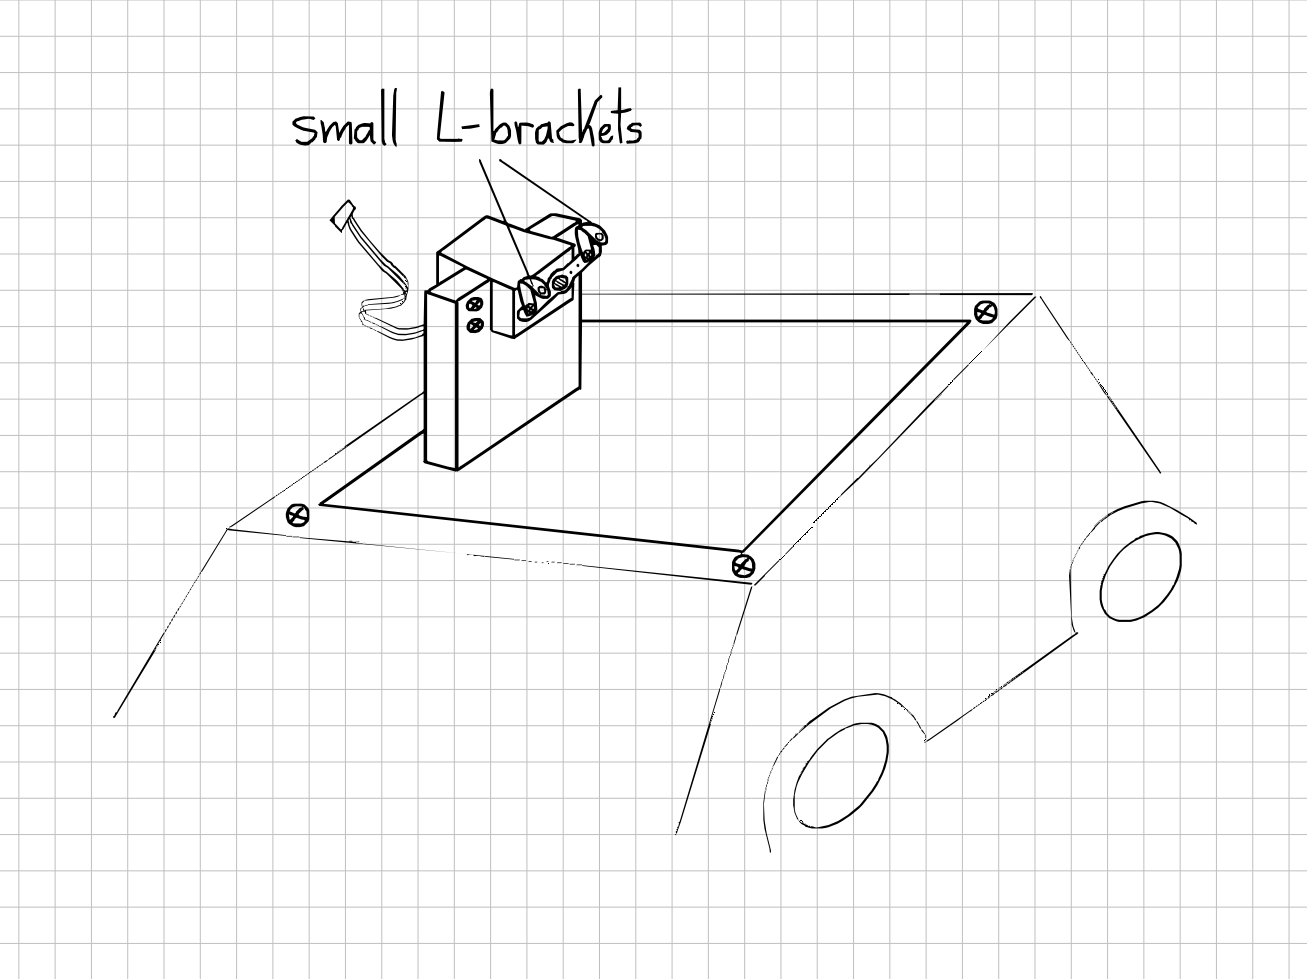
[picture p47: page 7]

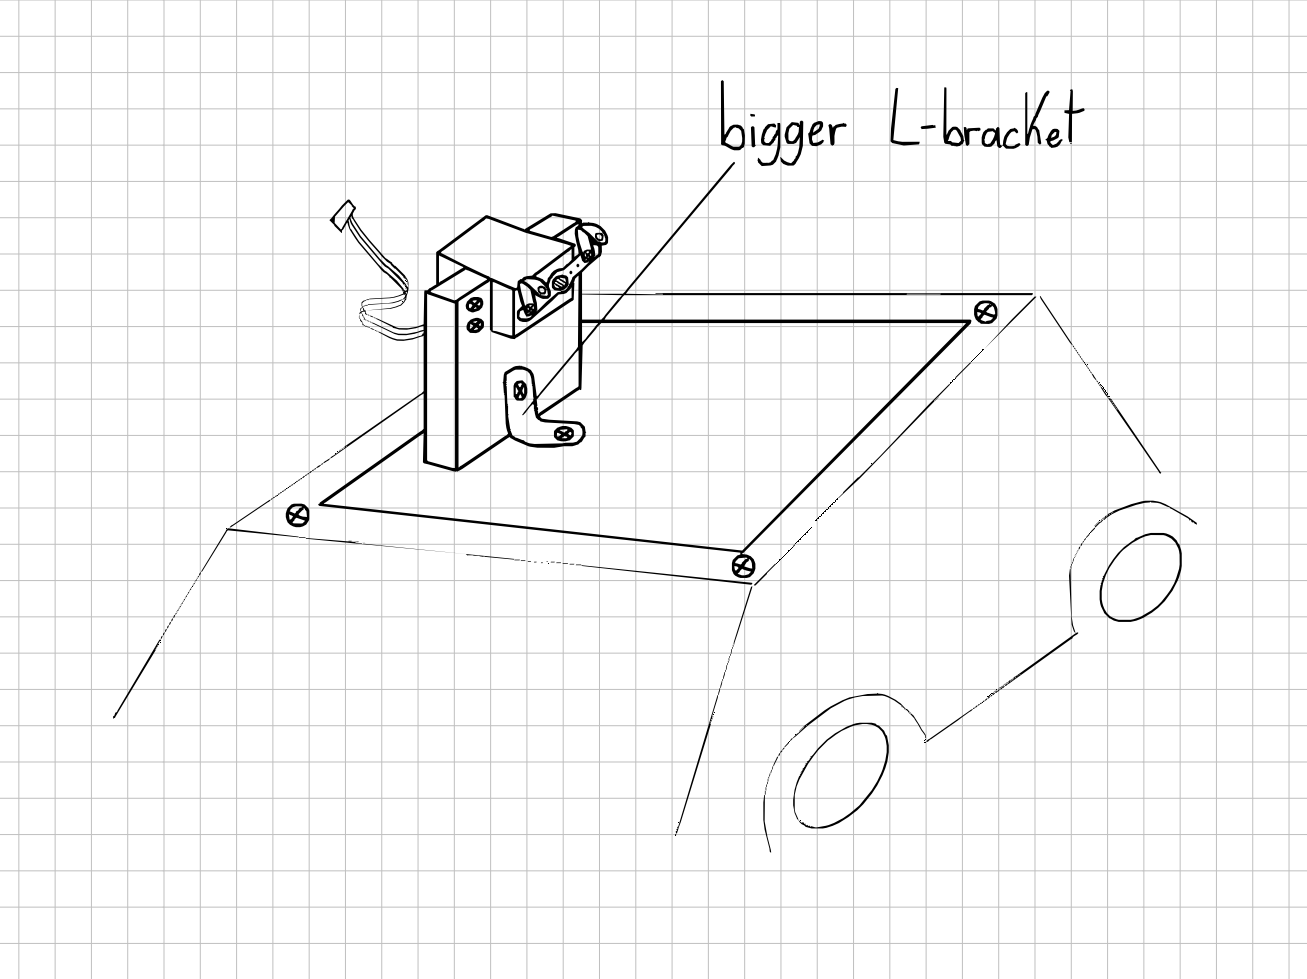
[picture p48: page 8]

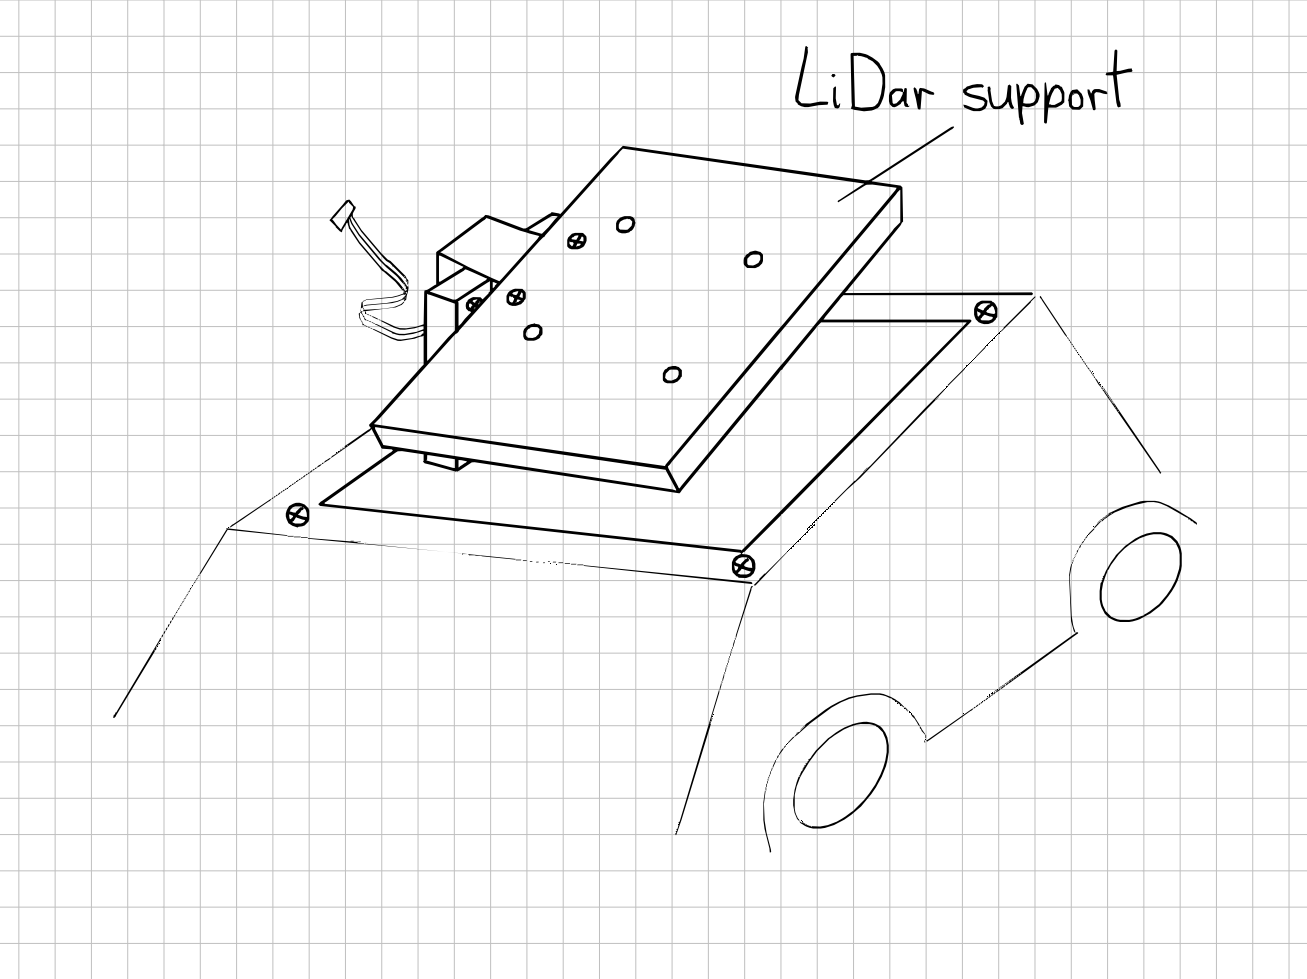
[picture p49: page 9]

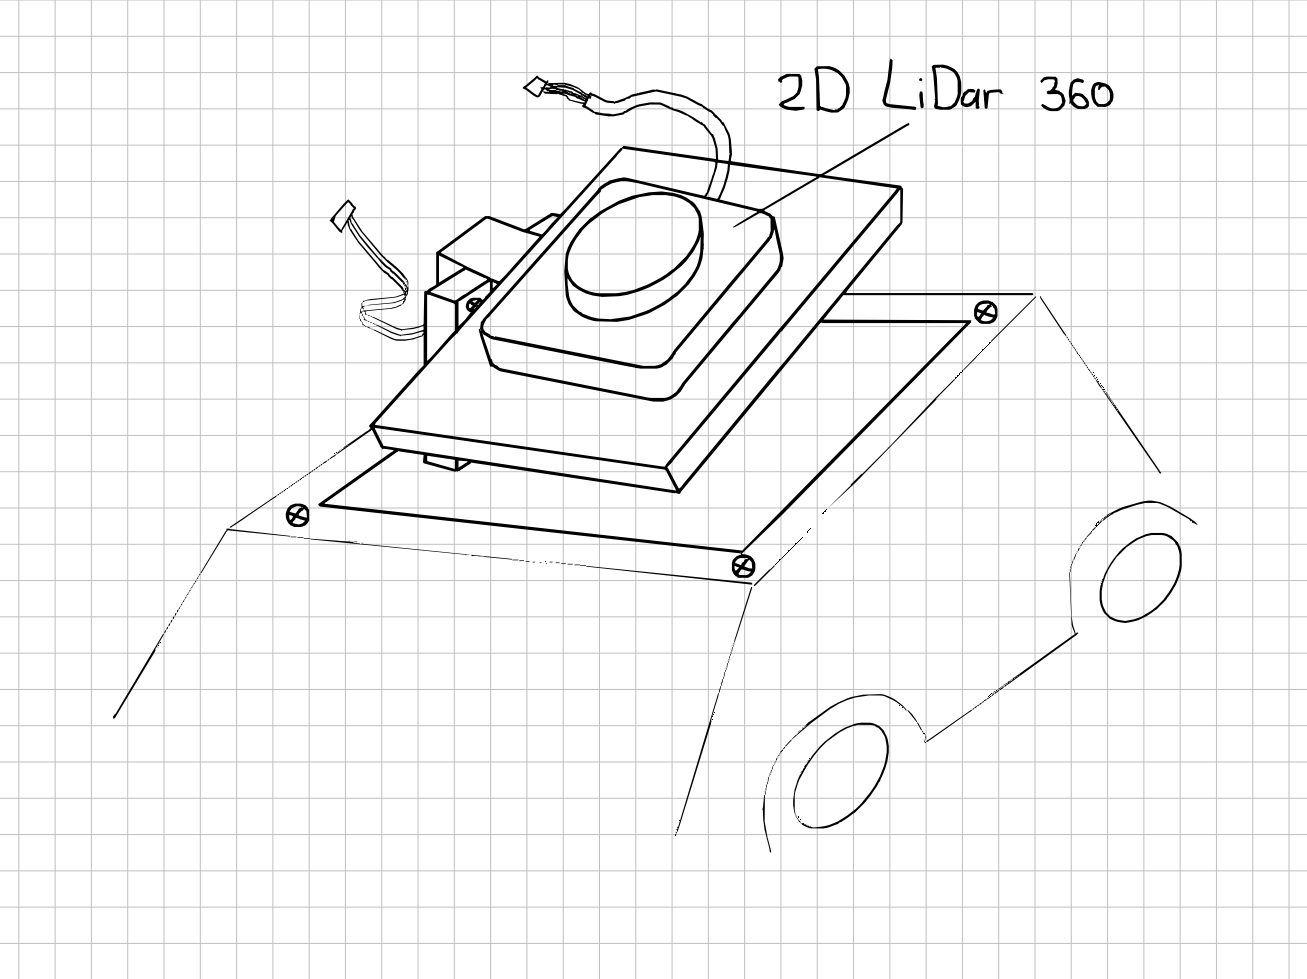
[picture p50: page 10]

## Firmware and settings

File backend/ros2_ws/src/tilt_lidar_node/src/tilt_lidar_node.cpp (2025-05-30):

#include <memory>
#include <cmath>
#include <string>

#include "rclcpp/rclcpp.hpp"
#include "std_msgs/msg/int32.hpp"
#include "sensor_msgs/msg/laser_scan.hpp"
#include "sensor_msgs/msg/point_cloud2.hpp"
#include "geometry_msgs/msg/transform_stamped.hpp"

#include "tf2_ros/buffer.h"
#include "tf2_ros/transform_listener.h"

#include "laser_geometry/laser_geometry.hpp"

using std::placeholders::_1;

class TiltLaserNode : public rclcpp::Node {
public:
  TiltLaserNode(const rclcpp::NodeOptions & options)
  : Node("tilt_laser_node", options),
    tf_buffer_(this->get_clock()),
    tf_listener_(tf_buffer_)
  {
    // Topics
    pointcloud_pub_ = create_publisher<sensor_msgs::msg::PointCloud2>("/point_cloud", 10);
    scan_sub_       = create_subscription<sensor_msgs::msg::LaserScan>(
                        "/scan", 10, std::bind(&TiltLaserNode::scanCallback, this, _1));
    servo_sub_      = create_subscription<std_msgs::msg::Int32>(
                        "/lidar_servo_angle", 10, std::bind(&TiltLaserNode::servoCallback, this, _1));

    // 1) Inject static mount: servo_frame → laser_frame
    {
      geometry_msgs::msg::TransformStamped mount_tf;
      mount_tf.header.frame_id    = "servo_frame";
      mount_tf.child_frame_id     = "laser_frame";
      mount_tf.header.stamp       = rclcpp::Time(0);  // static
      mount_tf.transform.translation.x = 0.0;
      mount_tf.transform.translation.y = 0.0;
      mount_tf.transform.translation.z = 0.04; // the lidar is 0.04m above the servo
      tf2::Quaternion q_mount;
      q_mount.setRPY(0,0,0);
      mount_tf.transform.rotation.x = q_mount.x();
      mount_tf.transform.rotation.y = q_mount.y();
      mount_tf.transform.rotation.z = q_mount.z();
      mount_tf.transform.rotation.w = q_mount.w();
      tf_buffer_.setTransform(mount_tf, "static_mount", true);
      RCLCPP_INFO(get_logger(),"Injected static mount servo_frame→laser_frame");
    }

    // 2) Inject initial servo tilt = 90° horizontal as base_link → servo_frame (static)
    //    (we treat 90° as “zero tilt” for horizontal)
    {
      current_servo_angle_deg_ = 90;
      geometry_msgs::msg::TransformStamped init_servo;
      init_servo.header.frame_id    = "base_link";
      init_servo.child_frame_id     = "servo_frame";
      init_servo.header.stamp       = rclcpp::Time(0);
      init_servo.transform.translation.x = 0.0;
      init_servo.transform.translation.y = 0.0;
      init_servo.transform.translation.z = 0.0;
      double a0 = (current_servo_angle_deg_ - 90.0) * M_PI/180.0;  // = 0
      tf2::Quaternion q0;
      q0.setRPY(0, a0, 0);
      init_servo.transform.rotation.x = q0.x();
      init_servo.transform.rotation.y = q0.y();
      init_servo.transform.rotation.z = q0.z();
      init_servo.transform.rotation.w = q0.w();
      tf_buffer_.setTransform(init_servo, "static_servo", true);
      RCLCPP_INFO(get_logger(),"Injected initial base_link→servo_frame @0 as horizontal");
    }

    RCLCPP_INFO(get_logger(),"TiltLaserNode started (servo=90°→horizontal)");
  }

private:
  void servoCallback(const std_msgs::msg::Int32::SharedPtr msg) {
    current_servo_angle_deg_ = msg->data;
  }

  void scanCallback(const sensor_msgs::msg::LaserScan::SharedPtr scan_msg) {
    // compute scan start/end in ROS time
    rclcpp::Time t_start(scan_msg->header.stamp);
    double dur = (scan_msg->time_increment > 0.0)
                 ? scan_msg->time_increment * scan_msg->ranges.size()
                 : scan_msg->scan_time;
    rclcpp::Time t_end = t_start + rclcpp::Duration::from_seconds(dur);

    RCLCPP_INFO(get_logger(),
                "scan@%.3f dur=%.3f → [%.3f]",
                t_start.seconds(), dur, t_end.seconds());

    // inject base_link→servo_frame at t_start and t_end with offset
    injectServoAt(t_start);
    injectServoAt(t_end);

    // check that base_link→laser_frame is now available at t_end
    if (!tf_buffer_.canTransform(
          "base_link", "laser_frame", t_end,
          rclcpp::Duration::from_seconds(0.0)))
    {
      RCLCPP_WARN(get_logger(),
                  "TF chain not ready at %.3f → skipping",
                  t_end.seconds());
      return;
    }

    // perform the high-fidelity projection
    sensor_msgs::msg::PointCloud2 cloud2;
    try {
      projector_.transformLaserScanToPointCloud(
        "base_link", *scan_msg, cloud2, tf_buffer_);
      RCLCPP_INFO(get_logger(),
                  "projected %zu points",
                  cloud2.width * cloud2.height);
    } catch (const tf2::TransformException & ex) {
      RCLCPP_ERROR(get_logger(),
                   "projection failed: %s", ex.what());
      return;
    }

    // publish the 3D cloud with the original scan timestamp
    cloud2.header.frame_id = "base_link";
    cloud2.header.stamp    = scan_msg->header.stamp;
    pointcloud_pub_->publish(cloud2);
    RCLCPP_INFO(get_logger(),
                "published PointCloud2 @ %.3f",
                t_start.seconds());
  }

  // helper: inject base_link→servo_frame at an arbitrary stamp, offset by -90°
  void injectServoAt(const rclcpp::Time & stamp) {
    geometry_msgs::msg::TransformStamped tf_msg;
    tf_msg.header.frame_id    = "base_link";
    tf_msg.child_frame_id     = "servo_frame";
    tf_msg.header.stamp       = stamp;
    tf_msg.transform.translation.x = 0.0;
    tf_msg.transform.translation.y = 0.0;
    tf_msg.transform.translation.z = 0.0;
    // subtract 90° so that servo=90°→horizontal=0 tilt
    double a = - (current_servo_angle_deg_ - 90.0) * M_PI/180.0; // - 90 degrees to have horizontal plane at 0 in base_link. and use - because of the direction of rotation
    tf2::Quaternion q;
    q.setRPY(0, a, 0);
    tf_msg.transform.rotation.x = q.x();
    tf_msg.transform.rotation.y = q.y();
    tf_msg.transform.rotation.z = q.z();
    tf_msg.transform.rotation.w = q.w();
    tf_buffer_.setTransform(tf_msg, "servo", false);
  }

  // Members
  rclcpp::Publisher<sensor_msgs::msg::PointCloud2>::SharedPtr pointcloud_pub_;
  rclcpp::Subscription<sensor_msgs::msg::LaserScan>::SharedPtr scan_sub_;
  rclcpp::Subscription<std_msgs::msg::Int32>::SharedPtr  servo_sub_;

  tf2_ros::Buffer           tf_buffer_;
  tf2_ros::TransformListener tf_listener_;

  laser_geometry::LaserProjection projector_;
  int current_servo_angle_deg_{90};
};

int main(int argc, char ** argv) {
  rclcpp::init(argc, argv);
  rclcpp::NodeOptions opts;
  opts.automatically_declare_parameters_from_overrides(true);
  auto node = std::make_shared<TiltLaserNode>(opts);
  rclcpp::spin(node);
  rclcpp::shutdown();
  return 0;
}

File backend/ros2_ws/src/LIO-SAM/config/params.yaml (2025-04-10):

/**:
  ros__parameters:

    # Topics
    pointCloudTopic: "points_raw"                   # Point cloud data
    imuTopic: "/imu_plugin/out"                        # IMU data
    odomTopic: "odometry/imu"                    # IMU pre-preintegration odometry, same frequency as IMU
    gpsTopic: "odometry/gpsz"                    # GPS odometry topic from navsat, see module_navsat.launch file

    # Frames
    lidarFrame: "velodyne_base_link"
    baselinkFrame: "base_footprint"
    odometryFrame: "odom"
    mapFrame: "map"

    # GPS Settings
    useImuHeadingInitialization: false           # if using GPS data, set to "true"
    useGpsElevation: false                       # if GPS elevation is bad, set to "false"
    gpsCovThreshold: 2.0                         # m^2, threshold for using GPS data
    poseCovThreshold: 25.0                       # m^2, threshold for using GPS data

    # Export settings
    savePCD: false                               # https://github.com/TixiaoShan/LIO-SAM/issues/3
    savePCDDirectory: "/Downloads/LOAM/"         # in your home folder, starts and ends with "/". Warning: the code deletes "LOAM" folder then recreates it. See "mapOptimization" for implementation

    # Sensor Settings
    sensor: velodyne                               # lidar sensor type, either 'velodyne', 'ouster' or 'livox'
    N_SCAN: 16                                   # number of lidar channels (i.e., Velodyne/Ouster: 16, 32, 64, 128, Livox Horizon: 6)
    Horizon_SCAN: 1800                            # lidar horizontal resolution (Velodyne:1800, Ouster:512,1024,2048, Livox Horizon: 4000)
    downsampleRate: 1                            # default: 1. Downsample your data if too many
    # points. i.e., 16 = 64 / 4, 16 = 16 / 1
    lidarMinRange: 1.0                           # default: 1.0, minimum lidar range to be used
    lidarMaxRange: 1000.0                        # default: 1000.0, maximum lidar range to be used

    # IMU Settings
    imuAccNoise: 3.9939570888238808e-03
    imuGyrNoise: 1.5636343949698187e-03
    imuAccBiasN: 6.4356659353532566e-05
    imuGyrBiasN: 3.5640318696367613e-05

    imuGravity: 9.80511
    imuRPYWeight: 0.01

    extrinsicTrans:  [ 0.0,  0.0,  -0.0103 ]
    #extrinsicRot:    [-1.0,  0.0,  0.0,
    #                   0.0,  1.0,  0.0,
    #                   0.0,  0.0, -1.0 ]
    #extrinsicRPY: [ 0.0,  1.0,  0.0,
    #               -1.0,  0.0,  0.0,
    #                0.0,  0.0,  1.0 ]
    extrinsicRot: [1.0, 0.0, 0.0,
                  0.0, 1.0, 0.0,
                  0.0, 0.0, 1.0]
    extrinsicRPY: [1.0, 0.0, 0.0,
                  0.0, 1.0, 0.0,
                  0.0, 0.0, 1.0]

    # LOAM feature threshold
    edgeThreshold: 1.0
    surfThreshold: 0.1
    edgeFeatureMinValidNum: 10
    surfFeatureMinValidNum: 100

    # voxel filter paprams
    odometrySurfLeafSize: 0.2                     # default: 0.4 - outdoor, 0.2 - indoor
    mappingCornerLeafSize: 0.1                    # default: 0.2 - outdoor, 0.1 - indoor
    mappingSurfLeafSize: 0.2                      # default: 0.4 - outdoor, 0.2 - indoor

    # robot motion constraint (in case you are using a 2D robot)
    z_tollerance: 1000.0                          # meters
    rotation_tollerance: 1000.0                   # radians

    # CPU Params
    numberOfCores: 4                              # number of cores for mapping optimization
    mappingProcessInterval: 0.15                  # seconds, regulate mapping frequency

    # Surrounding map
    surroundingkeyframeAddingDistThreshold: 1.0   # meters, regulate keyframe adding threshold
    surroundingkeyframeAddingAngleThreshold: 0.2  # radians, regulate keyframe adding threshold
    surroundingKeyframeDensity: 2.0               # meters, downsample surrounding keyframe poses   
    surroundingKeyframeSearchRadius: 50.0         # meters, within n meters scan-to-map optimization
    # (when loop closure disabled)

    # Loop closure
    loopClosureEnableFlag: true
    loopClosureFrequency: 1.0                     # Hz, regulate loop closure constraint add frequency
    surroundingKeyframeSize: 50                   # submap size (when loop closure enabled)
    historyKeyframeSearchRadius: 15.0             # meters, key frame that is within n meters from
    # current pose will be considerd for loop closure
    historyKeyframeSearchTimeDiff: 30.0           # seconds, key frame that is n seconds older will be
    # considered for loop closure
    historyKeyframeSearchNum: 25                  # number of hostory key frames will be fused into a
    # submap for loop closure
    historyKeyframeFitnessScore: 0.3              # icp threshold, the smaller the better alignment
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

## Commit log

2025-04-07 Add files via upload
    adding the stl files for the ultrasonic sensor mount.
    [bumper_and_carattach.stl, ultrasonicsensor_case.stl]
2025-04-07 Reorganized the stl files for the ultrasonic sensor
    [bumper_and_carattach.stl, ultrasonicsensor_case.stl]
2025-04-08 added micro-ROS working example (as a PlatformIO project) with ESP32 (WEMOS D1 R32)
2025-04-09 Reorganized files like requested and added a first incomplete version of webapp UI
    [bumper_and_carattach.stl, ultrasonicsensor_case.stl]
2025-04-09 working LIO-SAM algorithm with simulated Velodyne LiDAR in Gazebo
    [FRONT_LEFT_LINKSTL.stl, FRONT_RIGHT_LINKSTL.stl, HDL-32E.urdf.xacro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]
2025-04-16 Publish the CADs for the first prototype of a tilting lidar mount
    [basePlate.dxf, bearingSup.dxf, l-bracket by whatmakeart.stl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]
2025-04-16 Added 'layer_platform' folder with 3d step file for the layer platform, issue 46
    [layer-platform-v3.step]
2025-04-16 Added stl file and renamed files in snake_case
    [layer_platform.step, layer_platform.stl]
2025-04-16 Rename the files and add a copy of the whole design in the native .f3d format
    [l-bracket_by_whatmakeart.stl, lidar mount.step, lidar_mount.f3d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]
2025-04-17 adding encoder step file
    [encoder_support.step]
2025-04-29 Push the CADs for the lidar support (the real one)
    [basePlate.dxf, bearingSup.dxf, bearingSup.stl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]
2025-04-29 working udp connection using platformio and rplidar code example (lidar not tested yet)
2025-04-30 Added stl, step and f3d files for latest versions of the design
    [layer_platform_v1.step, layer_platform_v1.stl, layer_platform_v4.step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]
2025-05-01 new code for esp32 and lidar (uses a port of the SLAMTEC sdk to ESP32, only Serial communication for now for testing but trivially adaptable to previous UDP/microros example)
    TODO: builds without error but not tested yet
2025-05-10 lidar scan rosbag recording added
2025-05-10 sdk builds without error with esp32 s3
2025-05-12 serial monitor esp32 s3 working
2025-05-13 lidar working with microros over udp
2025-05-14 Update the layer platform to make the new components fit (and fix the holes for the lidar mount)
    [layer_platform_v6.f3d, layer_platform_v6.step, layer_platform_v6.stl]
2025-05-15 Added a case for the ESP32 S3, for it to stay fixed on the platform since it doesnt have any screw holes
    [esp32s3case.stl]
2025-05-16 xbox gamepad joystick publishing to ESP32 (motor control not done yet)
2025-05-20 merged code from loris, fixed orientation of point cloud
    [tilt_lidar_node.cpp]
2025-05-21 Push the design files of the two merged cases for the esp32-s3
    [esp32s3case.stl, esp32s3case_union.stl]
2025-05-22 add launch files for tilting lidar (one for live data and one that plays a bag file)
2025-05-23 Added the ultrasonic sensor emergency stop
2025-05-28 Push the first version of the Assembly section. Also update the component list and reorder sections in the readme.
2025-05-30 removed compilation error and added launch file
    [scanRegistration.cpp]
2025-05-30 matched loam topics with our namings, adapted the sweeping detection logic to use the servo angle directly
    TODO: debug and test frames and transforms and make Rviz output something
2025-05-30 added full (imu lidar servo) bad file, name is subset (sucks but whatever)
2025-05-30 use bag without IMU since it doesnt work
2025-05-30 ignore IMU in loam_back_and_forth
2025-05-30 change world to base_link frame
2025-05-30 add back models, add things in README
    [model-1_3.sdf, model-1_4.sdf, model.sdf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]
